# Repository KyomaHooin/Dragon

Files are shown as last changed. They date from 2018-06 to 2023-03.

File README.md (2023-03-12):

DESCRIPTION

DragonFrame Arduino code for custom stepper device.

DIAGRAM

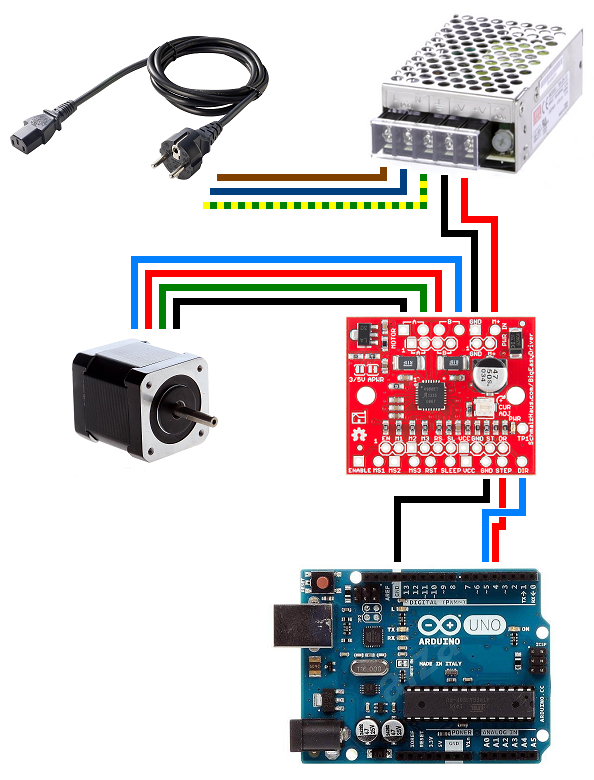
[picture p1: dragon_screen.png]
Dragon diagram


COMPONENT
<pre>
 1x <a href="https://laskarduino.cz/vyvojove-desky/100002-arduino-uno-r3-atmega328p-microusb-klon.html">Arduino Uno</a>(R3) 
 1x <a href="https://cnc.inshop.cz/krokove-motory-drivery/krokovy-motor-s-prirubou-nema17-0.44nm-typ-a">Nema 17 Stepper</a>(42STH47-1684A)
 1x <a href="https://www.aliexpress.com/item/2A-Phase-3D-Printer-Big-Easy-Driver-Board-V1-2-A4988-Stepper-Motor-Driver-Board-On/32834035739.html">Big Easy Driver</a>(ROB-12859) / <a href="https://arduino-shop.cz/arduino/1025-ramps1-4-drv8825-driver-pro-krokove-motory-1434305774.html">DRV8825</a> / (<a href="https://www.postavrobota.cz/Driver-pro-krokove-motory-A4988-d92.htm">A4988</a>)
 1x <a href="https://www.ges.cz/cz/zdroj-sitovy-prumyslovy-rs-25-12-GES07507650.html">Mean Well Supply</a> 12/2A(RS-25-12)
 3x <a href="https://www.ges.cz/cz/cpp-3-5-3bu-GES06614450.html">Terminal Block</a>(3BU 3.5mm)
 1x <a href="https://www.ges.cz/cz/nks-180-0-GES06914278.html">Supply Cable</a>
 1x <a href="http://www.hezkyden.cz/shop/hlinikovy-chladic-samolepici/">Driver Heatsink</a>(9x9x5mm)
10x <a href="https://www.ges.cz/cz/esst-m2-5x6-GES06814916.html">Screw Phillips Pan</a> M2.5x6(M2.5x4-5 = optimal)
 2x <a href="https://www.ges.cz/cz/skls-m3x6-GES06814931.html">Bolt Phillips Flat</a> M3x6(M3x4-5 = optimal)
 4x Screw Phillips Flat M3x30(M3x25 = optimal)
 5x <a href="https://www.ges.cz/cz/flexibilni-propojovaci-kabely-sd-j-10-GES07713790.html">Dupont cable</a>(MM)
 1x <a href="https://www.ges.cz/cz/mpfk-4-s-GES06900296.html">Phone 4Wire Flat</a>(1m)
 1x <a href="https://www.ges.cz/cz/wb-2x6-4bi-GES06614365.html">Coupler</a>(RJ11)
 2x <a href="https://www.ges.cz/cz/mp-6-4-GES06600690.html">Plug</a>(RJ11)
</pre>
FILE
<pre>
        openscad/ - Custom 3D printable box.
dragon_screen.png - Color connection schematic.
       DFMoco.ino - Original code by DragonFrame.
</pre>
SOURCE

https://github.com/KyomaHooin/Dragon

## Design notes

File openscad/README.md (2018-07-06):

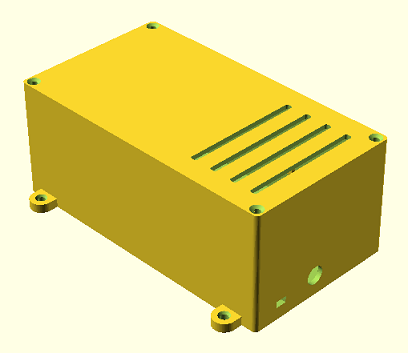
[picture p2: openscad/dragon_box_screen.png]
Dragon box


DESCRIPTION

DragonFrame Moco custom motor control box.

FILE
<pre>
              schema/ - Schematic directory.
          dragon.scad - SCAD model.
       dragon_top.stl - Top part STL.
    dragon_bottom.stl - Bottom part STL.
    dragon_bridge.stl - Bridge part STL.
dragon_box_screen.png - Box screenshot.
</pre>
SOURCE

https://github.com/KyomaHooin/Dragon

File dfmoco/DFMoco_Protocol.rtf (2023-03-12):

DFMoco Protocol

Version 2.0.0

Messages are given from perspective of DFMoco device.
Motor number starts at 1.
All positions are in steps. Dragonframe converts between step count and units.

Protocol
Serial Port (Comm)
Speed: 57600 Baud
Data bits: 8
Stop bits: 1
Parity: 0

Message Format
Messages are in ASCII text, with trailing \r\n

Messages

Hello (hi) - initiate communication
IN: hi
OUT: hi <major version> <number of axes> <full version string>
EXAMPLE: hi 1 8 1.2.7

Motor Status (ms) - check moving status of all motors
IN: ms
OUT: ms <0 or 1 for each motor, 1 = moving>
EXAMPLE: ms 10000000

Move Motor (mm) - move a motor to a position
IN: mm <motor> <step position>
EXAMPLE: mm 1 250
OUT: mm <motor> <target step position>
OUT2: mp <motor> <step position>
EXAMPLE: mm 1 250 (if motor needs to move)
EXAMPLE: mp 1 250 (if motor was already there)

Motor Position Query (mp) - request motor position
IN: mp <motor>
OUT: mp <motor> <step position>

Stop Motor (sm) - stop a motor fairly quickly
IN: sm <motor>
EXAMPLE: sm 1
OUT: sm <motor>
EXAMPLE: sm 1

Stop All (sa) - stop all motors fairly quickly
IN: sa
OUT: sa

Jog Motor (jm) - move the motor at a reasonable speed (pulse rate) towards destination
IN: jm <motor> <destination> [<velocity>]
OUT: jm <motor>

Note: velocity will be passed as a third argument if the major version in the hi response is 2 or greater. It is a positive number between 0 and 10000, with 10000 meaning to run at 100% of pulse rate.

Inch Motor (im) - move the in very small increments towards destination
IN: im <motor> <destination>
OUT: im <motor>

Pulse Rate (pr) - set the maximum steps/second of motor
IN: pr <motor> <steps/second>
EXAMPLE: pr 1 20000
OUT: pr <motor> <steps/second>

Zero Motor (zm) - resets the motor's current position to zero (no movement)
IN: zm <motor>
OUT: zm <motor>

New Position (np) - sets the motor's current position to a new value (no movement)
IN: np <motor> <position>
OUT: np <motor> <position>

Go-Motion (Blur):
This is complicated, and not required.
The goal is to capture a single frame, with the camera moving over a certain area while the shutter is open.

IN: bf <exposure time ms> <blur 0-1000> [ch#1 number] [ch#1 p0] [ch#1 p1] [ch#1 p2] [ch#2 number] [ch#2 p0] [ch#2 p1] [ch#2 p2] [etc]
OUT: bf 1000
Explanation:
The exposure time is how long the camera will be exposing the image.
The blur amount is in the range 0-1000, where 500 would correspond to a 50% or 180 degree blur setting (standard).
Then, for each motor that should move you receive four parameters:
1. A channel number.
2. A previous frame position value.
3. A current frame position value.
4. A next frame position value.

Each motor's movement should be centered around p1, such that:
The distance that is traveled is in relation to the blur percent (with 500 being 50%). 100% would mean the exposure happens for the entire distance of p0->p1->p2.
For 50% (the more standard case), the exposure happens at half the distance between p1 and the previous and next positions.
In mathematical terms, the exposure happens between these positions:
[p1 - (p1 - p0) * blurPercent] -> [p1] -> [p1 + (p2 - p1) * blurPercent]

And the exposure time should be evenly split between the two segments.
So it should take 1/2 of the exposure time to travel [p1 - (p1 - p0) * blurPercent] -> [p1] ,
and 1/2 of the exposure time to travel [p1] -> [p1 + (p2 - p1) * blurPercent]

Furthermore, there should be a ramp up to speed before the exposure starts, and a slow down after it stops.
The ramp up to speed should take exactly 1 second, even if the device does not need to move. This is so that Dragonframe knows when to trigger the camera.

After the device calculates the go-motion move, it starts sending all motors into the initial position.
Dragonframe will check for motor movement, and when everything has stopped, it will issue a "go" command:
IN: go
OUT: go

At this point the rig should immediately start the go-motion move as described above.

Notes
Any time a motor is moving, the device should send occasional "mp" messages.
Dragonframe will keep requesting motor status (ms) until the movement is finished.

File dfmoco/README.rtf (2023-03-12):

Simple Motion Control with Dragonframe (DFMoco)

Overview
This sketch turns an Arduino or equivalent development board into a multi-axis
motion control signal generator. It is for use with the Arc motion control system in
Dragonframe 4. It generates step and direction signals, which can be sent to
stepper motor drivers.

Note: This is NOT a REAL TIME solution.
This is a simple, low cost, motion control solution for stop motion and time-lapse.
Dragonframe will move all of your motors to position for frame 1, then shoot, then
move all of your motors to position for frame 2.

If you need real-time moves you should check out the DMC-32:
https://www.dragonframe.com/product/dmc-32/

Choosing a Development Board
Throughout this document we refer to Arduino because it is the most well-known
small development board. You can actually use a variety of boards:

To control up to four axes, you can use:
- Arduino Uno
- Arduino Duemilanove
- Arduino 101

To control up to eight axes, you can use:
- Arduino Mega
- Arduino Mega 2560

Wiring the Arduino for Motion Control
The Arduino running the DFMoco sketch will generate step and direction signals for stepper motors.

If you already have stepper motor drivers, you can take these signals and wire them into a connector for those drivers.

If you do not have stepper motor drivers, and need to move relatively small stepper motors, you can wire the Arduino signals to an Big Easy Driver or comparable board. You will use one Big Easy Driver for each stepper motor.
https://www.sparkfun.com/products/10735 (http://www.sparkfun.com/products/10267)

Kill Switch
It is recommended to incorporate a pushbutton kill switch, especially for larger rigs. This will stop all motors and bypasses any communication issues between the computer and the Arduino.

The DFMoco sketch expects you to have a kill switch attached to PIN 2 (interrupt 0).
If you do NOT want a kill switch, you must comment out this line in the code
#define KILL_SWITCH_INTERRUPT 0

You comment it out by add two forward slashes at the start, so it looks like this
//#define KILL_SWITCH_INTERRUPT 0

You can reference the schematic (but not the code) on this page if you are not sure how to connect a pushbutton:
https://docs.arduino.cc/built-in-examples/digital/Button

Step/Direction Pin Configuration

Channel 1
PIN 4 step
PIN 5 direction
Channel 2
PIN 6 step
PIN 7 direction
Channel 3
PIN 8 step
PIN 9 direction
Channel 4
PIN 10 step
PIN 11 direction

Channel 5
PIN 28 step
PIN 29 direction
Channel 6
PIN 30 step
PIN 31 direction
Channel 7
PIN 32 step
PIN 33 direction
Channel 8
PIN 34 step
PIN 35 direction

Install the Arduino Software
If you haven't already done so, you will need to install the Arduino software:
Go to https://www.arduino.cc/en/software and download the Arduino Software for your OS.

Loading the DFMoco Program
Once the Arduino software is installed, and your development board is wired, you need to load the DFMoco program
(called a sketch in Arduino terminology) onto the board.

1. Launch the IDE that you previously installed.
2. Open "DFMoco.ino" located in this folder.
3. Set your specific board using the "Tools" menu, "Board" submenu.
4. "Verify" the sketch by pressing the play button on the top left of the Arduino program.
(Command-R on Mac, Control-R on Windows)
5. "Upload" the sketch by pressing the button with a right arrow pointing to some dots.
(Command-U on Mac, Control-U on Windows)

Connecting Dragonframe and the Arduino Board
Your board is ready to go. Now you can start using it with Dragonframe:
1. Start Dragonframe.
2. Create a new scene or open a previous one.
3. Select Connections... from the Scene menu.
4. Press Add Connection and choose DFMoco Arduino as the device type.
5. Select ArcMoco #1 (or #2, #3, #4).
6. Choose the appropriate serial port.
7. Press the Connect button.
8. Refer to the Dragonframe User Guide, "Motion Control" chapter, and to our online tutorials for further instructions.

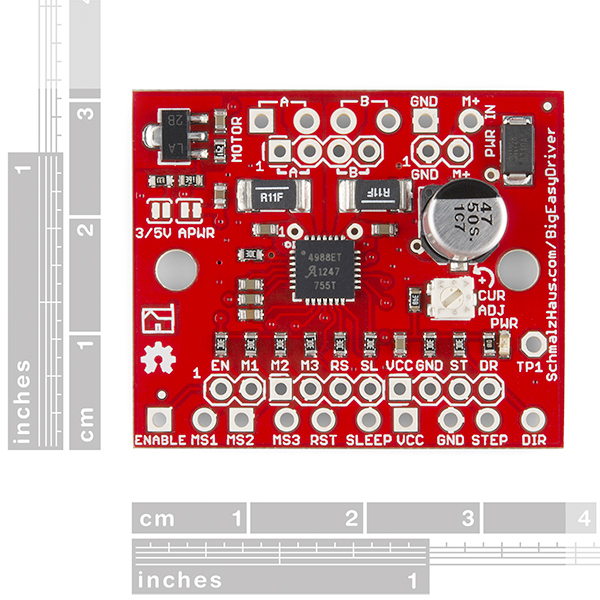
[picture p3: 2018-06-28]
openscad/schema/10735-02c.jpg

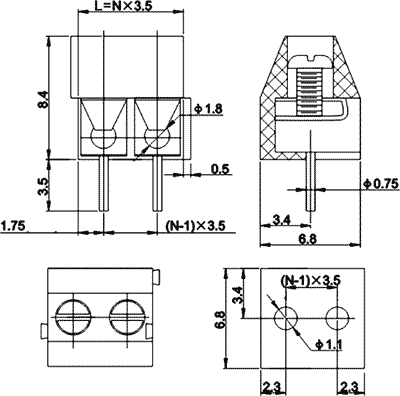
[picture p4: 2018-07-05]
openscad/schema/terminal.jpg

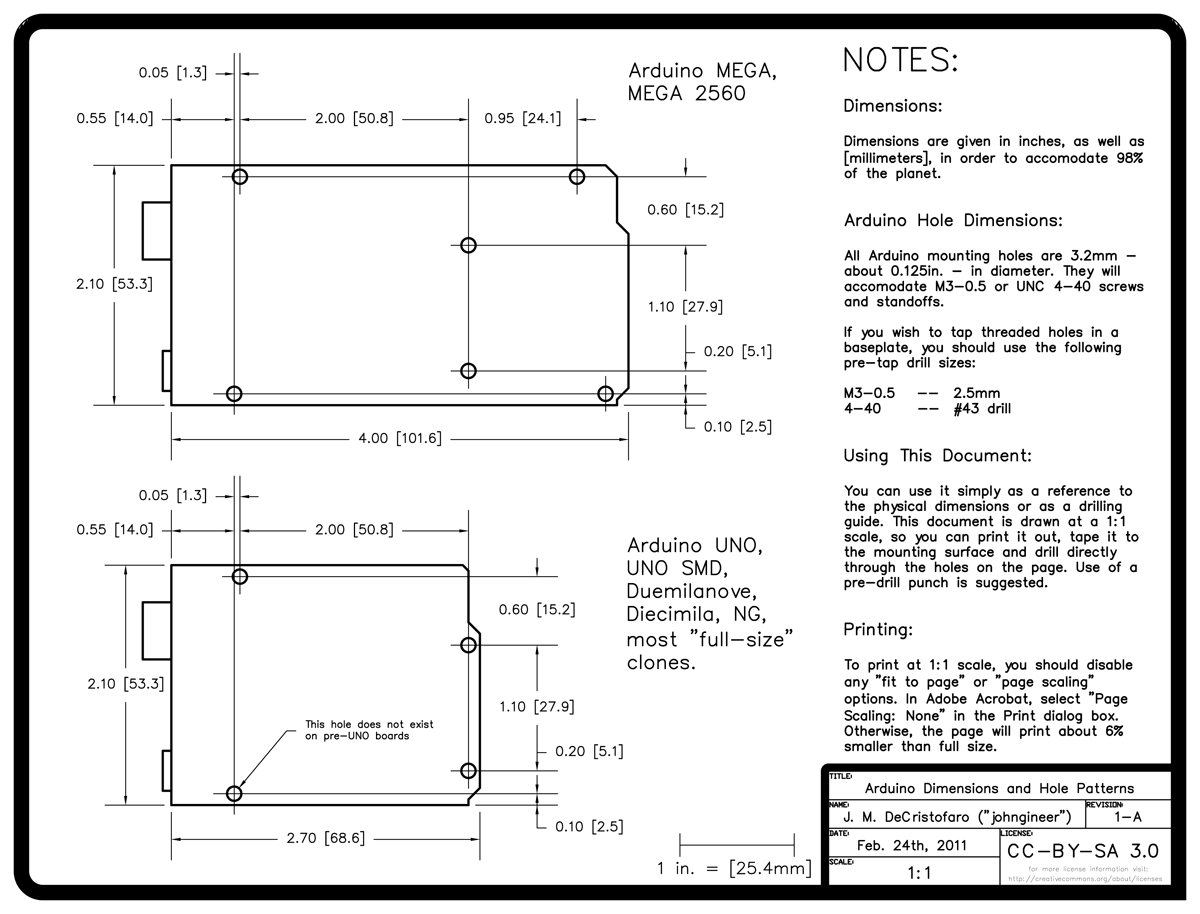
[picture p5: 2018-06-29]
openscad/schema/Arduino-Uno-Mega-Dimensions.png

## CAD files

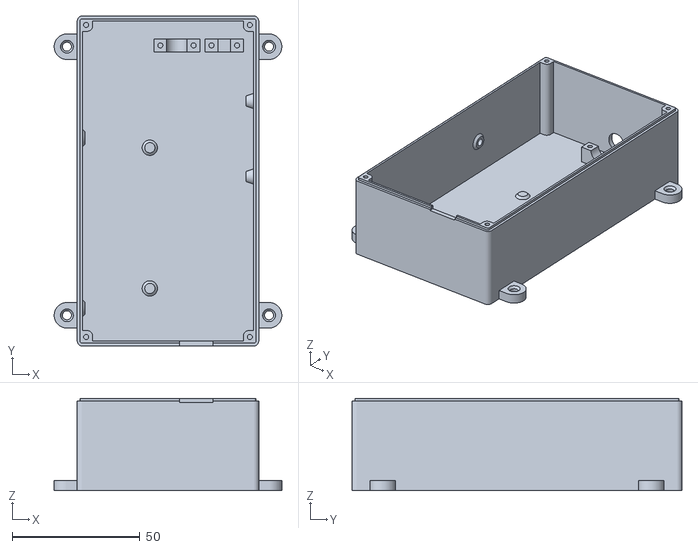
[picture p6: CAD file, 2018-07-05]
openscad/dragon_bottom.stl
89.0 x 129.0 x 36.0

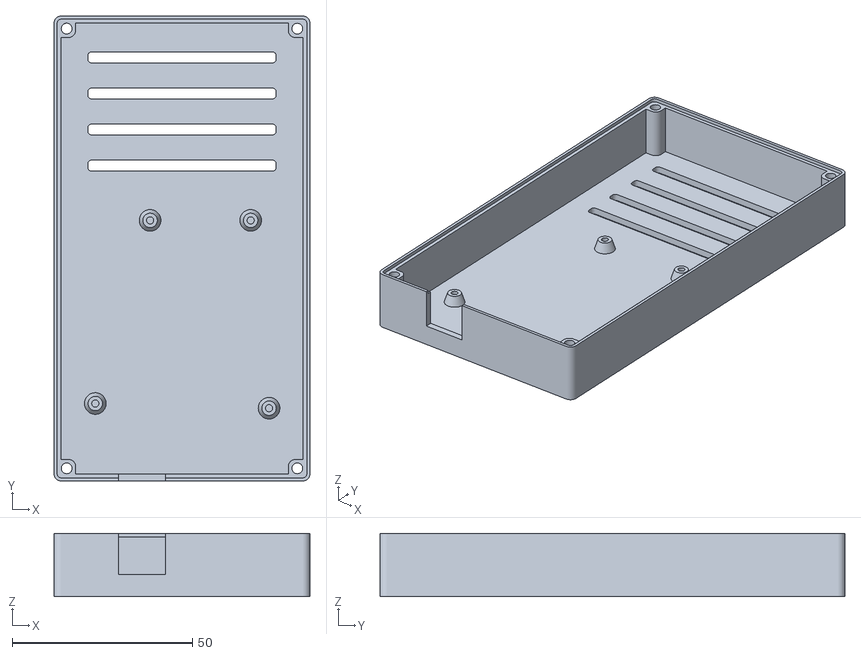
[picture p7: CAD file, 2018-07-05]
openscad/dragon_top.stl
71.0 x 129.0 x 17.5

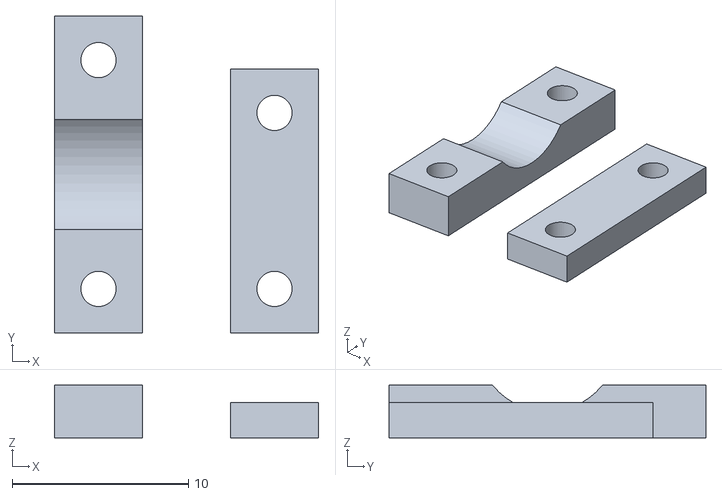
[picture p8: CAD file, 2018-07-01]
openscad/dragon_bridge.stl
15.0 x 18.0 x 3.00

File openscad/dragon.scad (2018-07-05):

//
// DragonFrame Motor Unit box
//

$fn=50;

drawTop=0;
drawBottom=0;
drawAll=0;
drawBridgePart=0;

//----------------------------

module rounded_rect(x, y, z, radius) {
    linear_extrude(height=z)
        minkowski() {
            square([x,y]);
            circle(r = radius);
        }
}

module mount(dia,thick) {
    difference() {
        cylinder(h=thick,d1=dia+4,d2=dia+2);
        translate([0,0,-1]) cylinder(h=thick+2,d=dia);
    }
}

module box_mount(thick,hole) {
    difference() {
    union() {
        cube([4,2,thick]);
        cube([2,4,thick]);
        translate([2,2,0]) cylinder(h=thick,d=4);
    }
    translate([1.5+0.01,1.5+0.01,-1]) cylinder(h=thick+2,d=hole);// Fold Bug
    }
}

module lip_lock_top() {
    rounded_rect(bottomX,bottomY,1,bottomThick/2+0.125);
}

module lip_lock_bottom() {
    difference() {
        rounded_rect(bottomX,bottomY,1,bottomThick);
        rounded_rect(bottomX,bottomY,1,bottomThick/2-0.125);
    }
}

module bridge() {
    difference() {
        cube([5,18,7]);
        translate([-1,9,7]) rotate([0,90,0]) cylinder(h=7,d=8);
        translate([2.5,2.5,3]) cylinder(h=5,d=2);
        translate([2.5,15.5,3]) cylinder(h=5,d=2);
    }
}

module bridge_motor() {
    difference() {
        cube([5,15,5]);
        translate([-1,5,3.5]) cube([7,5,2]);
        translate([2.5,2.5,1]) cylinder(h=5,d=2);
        translate([2.5,12.5,1]) cylinder(h=5,d=2);
    }
}

module bridge_part() {
    difference() {
        cube([5,18,3]);
        translate([-1,9,5.5]) rotate([0,90,0]) cylinder(h=7,d=8);
        translate([2.5,2.5,-1]) cylinder(h=5,d=2);
        translate([2.5,15.5,-1]) cylinder(h=5,d=2);
    }
    translate([10,0,0])
    difference() {
        cube([5,15,2]);
        translate([2.5,2.5,-1]) cylinder(h=5,d=2);
        translate([2.5,12.5,-1]) cylinder(h=5,d=2);
    }
}

module wall() {
    difference() {
        union() {
            cube([5,10,4]);
            translate([5,5,0]) cylinder(h=4,d=10);
        }
        translate([5,5,-1]) cylinder(h=6,d=3.5);
        translate([5,5,3])
        difference() {
            cylinder(h=1,d1=3.5,d2=5);
            cylinder(h=1,d=3.5);
        }
    }
}

module driver() {
    driverX=32;
    driverY=38;
    driverZ=1.3;
    difference() {
        color("darkgreen")
        translate([0,0,0]) cube([driverX,driverY,driverZ]);    
        translate([driverX/2,4.25,-1]) cylinder(h=driverZ+2,d=3);// Mount hole
        translate([driverX/2,driverY-4.25,-1]) cylinder(h=driverZ+2,d=3);
    }
    color("black") {
        translate([0,driverY/4,driverZ]) cube([6.6,22,8.4]);// Header M/PWR
        translate([driverX-6.6,driverY-11-driverY/8,driverZ]) cube([6.6,11,8.4]);// Header
    }
    color("silver")
    translate([driverX-20,driverY-8,driverZ]) cylinder(h=5.5,d=6);// Header
}

module uno() {
    unoX=53.3;
    unoY=68.6;
    unoZ=1.6;
    difference() {
        color("darkgreen")
        translate([0,0,0]) cube([unoX,unoY,unoZ]);    
        translate([unoX-2.5-5.1-27.9-15.2,14+1.3,-1]) cylinder(h=unoZ+2,d=3);// Mount Hole
        translate([unoX-2.5-5.1-27.9,14+1.3+50.8,-1]) cylinder(h=unoZ+2,d=3);
        translate([unoX-2.5-5.1,14+1.3+50.8,-1]) cylinder(h=unoZ+2,d=3);
        translate([unoX-2.5,14,-1]) cylinder(h=unoZ+2,d=3);
    }
    color("black") {
        translate([9.6-0.5,-6.2,unoZ-0.5]) cube([12+1,15,10.9+1]);// USB-B
        translate([unoX-2.5-5.1-27.9-15.2-2.54/2,25,unoZ]) cube([2.54,40,10]);// Header
        translate([unoX-2.5-2.54/2,35,unoZ]) cube([2.54,30,10]);
    }
}

module supply() {
    supplyX=51;
    supplyY=78;
    supplyZ=28;
    color("silver")
    translate([0,0,0]) cube([supplyX,supplyY,supplyZ]);
    color("black")
    translate([0,supplyY,supplyZ/4]) cube([51,14,14]);// Header
}

bottomX=65+2;
bottomY=125;
bottomZ=35;
bottomThick=2;

module bottom() {
    difference() {
        union() {
        difference() {
        translate([0,0,0]) rounded_rect(bottomX,bottomY,bottomZ+1,bottomThick);// BASE
        translate([0,0,bottomThick]) cube([bottomX,bottomY,bottomZ]);// FILL
        }
        translate([25.4+1,10.5+10,bottomThick]) cylinder(h=1,r1=3,r2=2);// Supply mount - bottom
        translate([25.4+1,10.5+55+10,bottomThick]) cylinder(h=1,r1=3,r2=2);
        }
        translate([-2,2.75+10,14+bottomThick+1]) rotate([0,90,0]) cylinder(h=4,d=3);
        translate([-2,2.75+66.5+10,14+bottomThick+1]) rotate([0,90,0]) cylinder(h=4,d=3);        
        translate([37,bottomY+2,bottomThick+7]) rotate([90,0,0]) cylinder(h=4,d=8);// Supply Hole
        translate([53,bottomY+2,bottomThick+3.5]) rotate([90,0,0]) cube([5,2.85,4]);// Motor Hole
        translate([0,0,bottomZ]) lip_lock_bottom();// Lip Lock
        translate([53.3+(topX-53.3)/2,6.2-bottomThick,bottomZ+topZ-topThick-3]) rotate([180,0,180]) uno();// Uno Cut
        translate([-bottomThick-0.1,2.75+10,14+bottomThick+1]) rotate([0,90,0]) cylinder(h=1.1,d1=5.5,d2=3);// Supply Sink
        translate([-bottomThick-0.1,2.75+66.5+10,14+bottomThick+1]) rotate([0,90,0]) cylinder(h=1.1,d1=5.5,d2=3);
    }
    translate([0-0.01,2.75+10,14+bottomThick+1]) rotate([0,90,0]) mount(3,1);// Supply mount - side
    translate([0-0.01,2.75+66.5+10,14+bottomThick+1]) rotate([0,90,0]) mount(3,1);
    translate([bottomX,60+4.25,16+bottomThick+9]) rotate([0,90,180]) mount(2,3);// Driver mount
    translate([bottomX,60+38-4.25,16+bottomThick+9]) rotate([0,90,180]) mount(2,3);
    translate([46,bottomY-12,bottomThick]) rotate([0,0,90]) bridge();// Supply Bridge
    translate([63,bottomY-12,bottomThick]) rotate([0,0,90]) bridge_motor();// Motor Bridge
    translate([0,0,2]) box_mount(bottomZ-1,2);// Bottom mount
    translate([bottomX,0,2]) rotate([0,0,90]) box_mount(bottomZ-1,2);
    translate([bottomX,bottomY,2]) rotate([0,0,180]) box_mount(bottomZ-1,2);
    translate([0-0.01,bottomY+0.01,2]) rotate([0,0,270]) box_mount(bottomZ-1,2);// NF Bug
    translate([bottomX+1,5,0]) wall();//Wall Mount
    translate([bottomX+1,bottomY-15,0]) wall();
    translate([-1,15,0]) rotate([0,0,180]) wall();
    translate([-1,bottomY-5,0]) rotate([0,0,180]) wall();
}

topX=65+2;
topY=125;
topZ=17.5;
topThick=2;
topUnoXOffset=(topX-53.3)/2;

module top() {
    difference() {
        translate([0,0,0]) rounded_rect(topX,topY,topZ,topThick);// BASE
        translate([0,0,-topThick]) cube([topX,topY,topZ]);// FILL
        translate([53.3+(topX-53.3)/2,6.2-topThick,topZ-topThick-3]) rotate([180,0,180]) uno();// Uno
        translate([1.5,1.5,topZ-3]) cylinder(h=topThick+2,d=3);//Top Mount Hole
        translate([topX-1.5,1.5,topZ-3]) cylinder(h=topThick+2,d=3);
        translate([1.5,topY-1.5,topZ-3]) cylinder(h=topThick+2,d=3);
        translate([topX-1.5,topY-1.5,topZ-3]) cylinder(h=topThick+2,d=3);
        for (vspace=[1:4])// Vent
            translate([topX/8,topY-10*vspace,topZ-topThick-1])rounded_rect(topX/8*6,1,topThick+2,1);
        translate(0,0,0) lip_lock_top();// Lip Lock
        translate([1.5,1.5,topZ-1]) cylinder(h=1,d1=3,d2=5.5);// Top Sink
        translate([topX-1.5,1.5,topZ-1]) cylinder(h=1,d1=3,d2=5.5);
        translate([1.5,topY-1.5,topZ-1]) cylinder(h=1,d1=3,d2=5.5);
        translate([topX-1.5,topY-1.5,topZ-1]) cylinder(h=1,d1=3,d2=5.5);
    }
    translate([2.5+topUnoXOffset,14+6.2-topThick,topZ-topThick]) rotate([0,180,0]) mount(2,3);// Uno Mount
    translate([2.5+5.1+topUnoXOffset,14+1.3+50.8+6.2-topThick,topZ-topThick]) rotate([0,180,0]) mount(2,3);
    translate([2.5+5.1+27.9+topUnoXOffset,14+1.3+50.8+6.2-topThick,topZ-topThick]) rotate([0,180,0]) mount(2,3);
    translate([2.5+5.1+27.9+15.2+topUnoXOffset,14+1.3+6.2-topThick,topZ-topThick]) rotate([0,180,0]) mount(2,3);
    translate([0,0,1]) box_mount(topZ-3,3);// Top Mount
    translate([topX,0,1]) rotate([0,0,90]) box_mount(topZ-3,3);
    translate([0,topY,1]) rotate([0,0,270]) box_mount(topZ-3,3);
    translate([topX+0.01,topY+0.02,1]) rotate([0,0,180]) box_mount(topZ-3,3);// strange bug?
}

//--------------------------

if (drawTop) {
    translate([topX+topThick,topThick,topZ]) rotate([0,180,0]) top();
}

if (drawBottom) {
    translate([bottomThick+9,bottomThick,0]) bottom();
}

if (drawBridgePart) {
    bridge_part();
}

if (drawAll) {
    bottom();
    translate([1,10,bottomThick+1]) supply();
    translate([bottomX-3,60,bottomThick+9]) rotate([0,0,0]) rotate([0,-90,0]) driver();
    translate([53.3+(topX-53.3)/2,6.2-bottomThick,bottomZ+topZ-topThick-3]) rotate([180,0,180]) uno();
    translate([0,0,bottomZ]) top();
}

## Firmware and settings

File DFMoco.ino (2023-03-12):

#define DFMOCO_VERSION 2
#define DFMOCO_VERSION_STRING "2.0.0"

/*
  DFMoco version 2.0.0
  
  Multi-axis motion control.
  For use with the Arc motion control system in Dragonframe 5.
  Generates step and direction signals, which can be sent to stepper motor drivers.
   
  Control up to four axes with an Uno, Duemilanove or 101 board.
  Control up to eight axes with a Mega or Mega 2560.

  Version History

  Version 2.0.0 Adds variable speed jogging for DF5
  Version 1.3.1 Report if go-motion speed cannot be reached.
  Version 1.3.0 Arduino 101 support. Remove non-Arduino support (chipKit, Maple).
  Version 1.2.7 Direction setup time.
  Version 1.2.6 Add PINOUT_VERSION option to use older pinout.
  Version 1.2.5 Fix jogging with low pulse rate.
  Version 1.2.4 Fix pin assignments
  Version 1.2.3 New Position command
  Version 1.2.2 Jog and Inch commands
  Version 1.2.1 Moved step/direction pins for motors 5-8.
                Detects board type automatically.
  Version 1.2.0 Basic go-motion capabilities
  Version 1.1.2 Smooth transitions when changing direction
  Version 1.1.1 Save/restore motor position
  Version 1.1.0 Major rework 
  Version 1.0.2 Moved pulses into interrupt handler
  Version 1.0.1 Added delay for pulse widths  
  Version 1.0.0 Initial public release.

  Getting Started:
  
   1. Install IDE (Integrated Development Environment):
      Go to https://www.arduino.cc/en/software and download the Arduino Software for your OS.
   2. Run the IDE you installed.
   3. Open this file in the IDE.
   4. Go to the Tools menu of the IDE and choose the Board type you are using.
   5. Verify/Compile the sketch. (Command-R on Mac, Control-R on Windows.)
   6. After this finishes, Upload the code to the board. (Command-U on Mac, Control-U on Windows.)
   

  Pin configuration:
  
  channel 1
        PIN   4   step
        PIN   5   direction
  channel 2
        PIN   6   step
        PIN   7   direction
  channel 3
        PIN   8   step
        PIN   9   direction
  channel 4
        PIN  10   step
        PIN  11   direction

  channel 5
        PIN  28   step
        PIN  29   direction
  channel 6
        PIN  30   step
        PIN  31   direction
  channel 7
        PIN  32   step
        PIN  33   direction
  channel 8
        PIN  34   step
        PIN  35   direction
 */

// change this to 1 if you want original pinout for channels 5-8
#define PINOUT_VERSION 2

/*
  This is PINOUT_VERSION 1
  
  channel 5
        PIN  22   step
        PIN  23   direction
  channel 6
        PIN  24   step
        PIN  25   direction
  channel 7
        PIN  26   step
        PIN  27   direction
  channel 8
        PIN  28   step
        PIN  29   direction
*/

// detect board type
#if defined(__AVR_ATmega1280__) || defined(__AVR_ATmega2560__)
  #define BOARD_MEGA 1
#elif defined(__AVR_ATmega328P__) || defined(__AVR_ATmega328__)  || defined(__AVR_ATmega168__)
  #define BOARD_UNO 1
#elif defined(ARDUINO_ARCH_ARC32) // Intel Curie/101
  #define BOARD_101 1
  #include "CurieTimerOne.h"
#else
  #error Cannot identify board
#endif

// USER: if you want a kill switch, uncomment out the next line by removing the // characters
//#define KILL_SWITCH_INTERRUPT 0

#define SERIAL_DEVICE Serial

#if defined(BOARD_101)
  #define PIN_ON(port, pin)  { digitalWrite(pin, 1); }
  #define PIN_OFF(port, pin) { digitalWrite(pin, 0); }
#else
  #define PIN_ON(port, pin)  { port |= pin; }
  #define PIN_OFF(port, pin) { port &= ~pin; }
#endif

// Arduino Uno/Duemilanove  -> 4 MOTORS MAX
// Arduino Mega 2560 / Mega -> 8 MOTORS MAX
#if defined(BOARD_UNO) || defined(BOARD_101)
#define MOTOR_COUNT 4
#else
#define MOTOR_COUNT 8
#endif

#define TIME_CHUNK 50
#define SEND_POSITION_COUNT 20000

// update velocities 20 x second
#define VELOCITY_UPDATE_RATE (50000 / TIME_CHUNK)
#define VELOCITY_INC(maxrate) (max(1.0f, maxrate / 70.0f))
#define VELOCITY_CONVERSION_FACTOR 0.30517578125f /* 20 / 65.536f */

#define MAX_VELOCITY 20000

// setup step and direction pins
#if defined(BOARD_101)

  #define MOTOR0_STEP_PORT 0
  #define MOTOR0_STEP_PIN  4
  
  #define MOTOR1_STEP_PORT 0
  #define MOTOR1_STEP_PIN  6

  #define MOTOR2_STEP_PORT 0
  #define MOTOR2_STEP_PIN  8

  #define MOTOR3_STEP_PORT 0
  #define MOTOR3_STEP_PIN  10

#elif defined(__AVR_ATmega1280__) || defined(__AVR_ATmega2560__)

  #define MOTOR0_STEP_PORT PORTG
  #define MOTOR0_STEP_PIN  B00100000
  
  #define MOTOR1_STEP_PORT PORTH
  #define MOTOR1_STEP_PIN  B00001000

  #define MOTOR2_STEP_PORT PORTH
  #define MOTOR2_STEP_PIN  B00100000

  #define MOTOR3_STEP_PORT PORTB
  #define MOTOR3_STEP_PIN  B00010000

  #if ( PINOUT_VERSION == 2 )
  
    #define MOTOR4_STEP_PORT PORTA
    #define MOTOR4_STEP_PIN  B01000000
  
    #define MOTOR5_STEP_PORT PORTC
    #define MOTOR5_STEP_PIN  B10000000
  
    #define MOTOR6_STEP_PORT PORTC
    #define MOTOR6_STEP_PIN  B00100000
  
    #define MOTOR7_STEP_PORT PORTC
    #define MOTOR7_STEP_PIN  B00001000

  #elif ( PINOUT_VERSION == 1 )
  
    #define MOTOR4_STEP_PORT PORTA
    #define MOTOR4_STEP_PIN  B00000001
  
    #define MOTOR5_STEP_PORT PORTA
    #define MOTOR5_STEP_PIN  B00000100
  
    #define MOTOR6_STEP_PORT PORTA
    #define MOTOR6_STEP_PIN  B00010000
  
    #define MOTOR7_STEP_PORT PORTA
    #define MOTOR7_STEP_PIN  B01000000

  #endif

#elif defined(BOARD_UNO)

  #define MOTOR0_STEP_PORT PORTD
  #define MOTOR0_STEP_PIN  B00010000
  
  #define MOTOR1_STEP_PORT PORTD
  #define MOTOR1_STEP_PIN  B01000000

  #define MOTOR2_STEP_PORT PORTB
  #define MOTOR2_STEP_PIN  B00000001

  #define MOTOR3_STEP_PORT PORTB
  #define MOTOR3_STEP_PIN  B00000100

#endif



/**
 * Serial output specialization
 */
#if defined(UBRRH)
#define TX_UCSRA UCSRA
#define TX_UDRE  UDRE
#define TX_UDR   UDR
#else
#define TX_UCSRA UCSR0A
#define TX_UDRE  UDRE0
#define TX_UDR   UDR0
#endif
 
char txBuf[32];
char *txBufPtr;

#define TX_MSG_BUF_SIZE 16

#define MSG_STATE_START 0
#define MSG_STATE_CMD   1
#define MSG_STATE_DATA  2
#define MSG_STATE_ERR   3

#define MSG_STATE_DONE  100

/*
 * Command codes from user
 */
#define USER_CMD_ARGS 40

#define CMD_NONE       0
#define CMD_HI         10
#define CMD_MS         30
#define CMD_NP         31
#define CMD_MM         40 // move motor
#define CMD_PR         41 // pulse rate
#define CMD_SM         42 // stop motor
#define CMD_MP         43 // motor position
#define CMD_ZM         44 // zero motor
#define CMD_SA         50 // stop all (hard)
#define CMD_BF         60 // blur frame
#define CMD_GO         61 // go!

#define CMD_JM         70 // jog motor
#define CMD_IM         71 // inch motor


#define MSG_HI 01
#define MSG_MM 02
#define MSG_MP 03
#define MSG_MS 04
#define MSG_PR 05
#define MSG_SM 06
#define MSG_SA 07
#define MSG_BF 10
#define MSG_GO 11
#define MSG_JM 12
#define MSG_IM 13


struct UserCmd
{
  byte command;
  byte argCount;
  int32_t args[USER_CMD_ARGS];
} ;

/*
 * Message state machine variables.
 */
byte lastUserData;
int  msgState;
int  msgNumberSign;
UserCmd userCmd;


struct txMsg
{
  byte msg;
  byte motor;
};

struct TxMsgBuffer
{
  txMsg buffer[TX_MSG_BUF_SIZE];
  byte head;
  byte tail;
};

TxMsgBuffer txMsgBuffer;


/*
 Motor data.
 */

uint16_t           motorAccumulator0;
uint16_t           motorAccumulator1;
uint16_t           motorAccumulator2;
uint16_t           motorAccumulator3;
#if MOTOR_COUNT > 4
uint16_t           motorAccumulator4;
uint16_t           motorAccumulator5;
uint16_t           motorAccumulator6;
uint16_t           motorAccumulator7;
#endif
uint16_t*          motorAccumulator[MOTOR_COUNT] =
{
  &motorAccumulator0, &motorAccumulator1, &motorAccumulator2, &motorAccumulator3, 
#if MOTOR_COUNT > 4
  &motorAccumulator4, &motorAccumulator5, &motorAccumulator6, &motorAccumulator7 
#endif
};

uint16_t           motorMoveSteps0;
uint16_t           motorMoveSteps1;
uint16_t           motorMoveSteps2;
uint16_t           motorMoveSteps3;
#if MOTOR_COUNT > 4
uint16_t           motorMoveSteps4;
uint16_t           motorMoveSteps5;
uint16_t           motorMoveSteps6;
uint16_t           motorMoveSteps7;
#endif
uint16_t*          motorMoveSteps[MOTOR_COUNT] =
{
  &motorMoveSteps0, &motorMoveSteps1, &motorMoveSteps2, &motorMoveSteps3,
#if MOTOR_COUNT > 4
  &motorMoveSteps4, &motorMoveSteps5, &motorMoveSteps6, &motorMoveSteps7
#endif
};


uint16_t           motorMoveSpeed0;
uint16_t           motorMoveSpeed1;
uint16_t           motorMoveSpeed2;
uint16_t           motorMoveSpeed3;
#if MOTOR_COUNT > 4
uint16_t           motorMoveSpeed4;
uint16_t           motorMoveSpeed5;
uint16_t           motorMoveSpeed6;
uint16_t           motorMoveSpeed7;
#endif
uint16_t         * motorMoveSpeed[MOTOR_COUNT] =
{
  &motorMoveSpeed0, &motorMoveSpeed1, &motorMoveSpeed2, &motorMoveSpeed3,
#if MOTOR_COUNT > 4
  &motorMoveSpeed4, &motorMoveSpeed5, &motorMoveSpeed6, &motorMoveSpeed7
#endif
};

volatile boolean nextMoveLoaded;


unsigned int   velocityUpdateCounter;
byte           sendPositionCounter;
boolean        hardStopRequested;

byte sendPosition = 0;
byte motorMoving = 0;
byte toggleStep = 0;


#define P2P_MOVE_COUNT 7

struct Motor
{
  byte   stepPin;
  byte   dirPin;

  // pre-computed move
  float   moveTime[P2P_MOVE_COUNT];
  int32_t movePosition[P2P_MOVE_COUNT];
  float   moveVelocity[P2P_MOVE_COUNT];
  float   moveAcceleration[P2P_MOVE_COUNT];

  float   gomoMoveTime[P2P_MOVE_COUNT];
  int32_t gomoMovePosition[P2P_MOVE_COUNT];
  float   gomoMoveVelocity[P2P_MOVE_COUNT];
  float   gomoMoveAcceleration[P2P_MOVE_COUNT];

  int       currentMove;
  float     currentMoveTime;
  
  volatile  boolean   dir;

  int32_t   position;
  int32_t   destination;
  float     maxVelocity;
  float     maxAcceleration;
  
  uint16_t  nextMotorMoveSteps;
  float     nextMotorMoveSpeed;

};

boolean goMoReady;
int     goMoDelayTime;

Motor motors[MOTOR_COUNT];

#ifdef KILL_SWITCH_INTERRUPT
void killSwitch()
{
  hardStopRequested = true;
}
#endif
      
/*
 * setup() gets called once, at the start of the program.
 */
void setup()
{
  goMoReady = false;
  lastUserData = 0;
  msgState = MSG_STATE_START;
  velocityUpdateCounter = 0;
  sendPositionCounter = 10;
  nextMoveLoaded = false;
  hardStopRequested = false;

  for (int i = 0; i < 32; i++)
    txBuf[i] = 0;
  
  txBufPtr = txBuf;
  
  #ifdef KILL_SWITCH_INTERRUPT
  attachInterrupt(KILL_SWITCH_INTERRUPT, killSwitch, CHANGE);
  #endif
  
  // initialize motor structures
  for (int i = 0; i < MOTOR_COUNT; i++)
  {
    // setup motor pins - you can customize/modify these after loop
    // default sets step/dir pairs together, with first four motors at 4/5, 6/7, 8/9, 10/11
    // then, for the Mega boards, it jumps to 28/29, 30/31, 32/33, 34/35
    #if ( PINOUT_VERSION == 2 )
      motors[i].stepPin = (i * 2) + ( (i < 4) ? 4 : 20 );
    #elif ( PINOUT_VERSION == 1 )
      motors[i].stepPin = (i * 2) + ( (i < 4) ? 4 : 14 );
    #endif
    
    motors[i].dirPin = motors[i].stepPin + 1;
    motors[i].dir = true; // forward
    motors[i].position = 0L;
    motors[i].destination = 0L;

    motors[i].nextMotorMoveSteps = 0;
    motors[i].nextMotorMoveSpeed = 0;
    
    setPulsesPerSecond(i, 5000);
  }


  // set output pins
  for (int i = 0; i < MOTOR_COUNT; i++)
  {
    pinMode(motors[i].stepPin, OUTPUT);
    pinMode(motors[i].dirPin, OUTPUT);
    
#if defined(__AVR_ATmega1280__) || defined(__AVR_ATmega2560__)

    // disable PWM
    switch (motors[i].stepPin)
    {
      #if defined(TCCR3A) && defined(COM3B1)
      case 4:
        TCCR3A &= ~COM3B1;
        break;
      #endif

      #if defined(TCCR4A) && defined(COM4A1)
      case 6:
        TCCR4A &= ~COM4A1;
        break;
      #endif

      #if defined(TCCR4A) && defined(COM4C1)
      case 8:
        TCCR4A &= ~COM4C1;
        break;
      #endif

      #if defined(TCCR2A) && defined(COM2A1)
      case 10:
        TCCR2A &= ~COM2A1;
        break;
      #endif
    }
    
#else
    
    switch (motors[i].stepPin)
    {
      #if defined(TCCR1A) && defined(COM1B1)
      case 10:
        TCCR1A &= ~COM1B1;
        break;
      #endif

    }

#endif
  }
  
  // set initial direction
  for (int i = 0; i < MOTOR_COUNT; i++)
  {
    digitalWrite( motors[i].dirPin, motors[i].dir ? HIGH : LOW );
  }

  // setup serial connection
  Serial.begin(57600);

  sendMessage(MSG_HI, 0);
    
  // SET UP interrupt timer  
  #if defined(BOARD_UNO) || defined(BOARD_MEGA)

    TCCR1A = 0;
    TCCR1B = _BV(WGM13);
  
    ICR1 = (F_CPU / 4000000) * TIME_CHUNK; // goes twice as often as time chunk, but every other event turns off pins
    TCCR1B &= ~(_BV(CS10) | _BV(CS11) | _BV(CS12));
    TIMSK1 = _BV(TOIE1);
    TCCR1B |= _BV(CS10);

  #elif defined(BOARD_101)

    CurieTimerOne.start(25, &updateStepDirection);

  #endif
}

#if defined(BOARD_101)
void updateStepDirection(void)
{
#else
ISR(TIMER1_OVF_vect)
{
#endif

  toggleStep = !toggleStep;
  
  if (toggleStep)
  {
    // MOTOR 1
    if (motorMoveSteps0)
    {
      uint16_t a = motorAccumulator0;
      motorAccumulator0 += motorMoveSpeed0;
      if (motorAccumulator0 < a)
      {
        motorMoveSteps0--;
        
        PIN_ON(MOTOR0_STEP_PORT, MOTOR0_STEP_PIN);
      }
    }

    // MOTOR 2
    if (motorMoveSteps1)
    {
      uint16_t a = motorAccumulator1;
      motorAccumulator1 += motorMoveSpeed1;
      if (motorAccumulator1 < a)
      {
        motorMoveSteps1--;
        
        PIN_ON(MOTOR1_STEP_PORT, MOTOR1_STEP_PIN);
      }
    }

    // MOTOR 3
    if (motorMoveSteps2)
    {
      uint16_t a = motorAccumulator2;
      motorAccumulator2 += motorMoveSpeed2;
      if (motorAccumulator2 < a)
      {
        motorMoveSteps2--;
        
        PIN_ON(MOTOR2_STEP_PORT, MOTOR2_STEP_PIN);
      }
    }

    // MOTOR 4
    if (motorMoveSteps3)
    {
      uint16_t a = motorAccumulator3;
      motorAccumulator3 += motorMoveSpeed3;
      if (motorAccumulator3 < a)
      {
        motorMoveSteps3--;
        
        PIN_ON(MOTOR3_STEP_PORT, MOTOR3_STEP_PIN);
      }
    }

#if MOTOR_COUNT > 4

    // MOTOR 5
    if (motorMoveSteps4)
    {
      uint16_t a = motorAccumulator4;
      motorAccumulator4 += motorMoveSpeed4;
      if (motorAccumulator4 < a)
      {
        motorMoveSteps4--;
        
        PIN_ON(MOTOR4_STEP_PORT, MOTOR4_STEP_PIN);
      }
    }

    // MOTOR 6
    if (motorMoveSteps5)
    {
      uint16_t a = motorAccumulator5;
      motorAccumulator5 += motorMoveSpeed5;
      if (motorAccumulator5 < a)
      {
        motorMoveSteps5--;
        
        PIN_ON(MOTOR5_STEP_PORT, MOTOR5_STEP_PIN);
      }
    }

    // MOTOR 7
    if (motorMoveSteps6)
    {
      uint16_t a = motorAccumulator6;
      motorAccumulator6 += motorMoveSpeed6;
      if (motorAccumulator6 < a)
      {
        motorMoveSteps6--;
        
        PIN_ON(MOTOR6_STEP_PORT, MOTOR6_STEP_PIN);
      }
    }

    // MOTOR 8
    if (motorMoveSteps7)
    {
      uint16_t a = motorAccumulator7;
      motorAccumulator7 += motorMoveSpeed7;
      if (motorAccumulator7 < a)
      {
        motorMoveSteps7--;
        
        PIN_ON(MOTOR7_STEP_PORT, MOTOR7_STEP_PIN);
      }
    }

#endif

  }
  else
  {
    velocityUpdateCounter++;
    if (velocityUpdateCounter == VELOCITY_UPDATE_RATE)
    {
      velocityUpdateCounter = 0;
      
      if (sendPositionCounter)
      {
        sendPositionCounter--;
      }
      
      for (int i = 0; i < MOTOR_COUNT; i++)
      {
        if (*motorMoveSpeed[i] && !motors[i].nextMotorMoveSpeed)
        {
          bitSet(sendPosition, i);
        }

        *motorMoveSteps[i] = motors[i].nextMotorMoveSteps;
        *motorMoveSpeed[i] = motors[i].nextMotorMoveSpeed;
        digitalWrite(motors[i].dirPin, motors[i].dir);

        *motorAccumulator[i] = 65535;
      }
      nextMoveLoaded = false; // ready for new move
    }
    
    PIN_OFF(MOTOR0_STEP_PORT, MOTOR0_STEP_PIN);
    PIN_OFF(MOTOR1_STEP_PORT, MOTOR1_STEP_PIN);
    PIN_OFF(MOTOR2_STEP_PORT, MOTOR2_STEP_PIN);
    PIN_OFF(MOTOR3_STEP_PORT, MOTOR3_STEP_PIN);

    #if MOTOR_COUNT > 4
      PIN_OFF(MOTOR4_STEP_PORT, MOTOR4_STEP_PIN);
      PIN_OFF(MOTOR5_STEP_PORT, MOTOR5_STEP_PIN);
      PIN_OFF(MOTOR6_STEP_PORT, MOTOR6_STEP_PIN);
      PIN_OFF(MOTOR7_STEP_PORT, MOTOR7_STEP_PIN);
    #endif
  }
}

/*
 * For stepper-motor timing, every clock cycle counts.
 */
void loop()
{
  int32_t *ramValues = (int32_t *)malloc(sizeof(int32_t) * MOTOR_COUNT);
  int32_t *ramNotValues = (int32_t *)malloc(sizeof(int32_t) * MOTOR_COUNT);

  for (int i = 0; i < MOTOR_COUNT; i++)
  { 
    if (ramValues[i] == ~ramNotValues[i])
    {
      motors[i].position = motors[i].destination = ramValues[i];
    }
  }  

  while (true)
  {
    if (!nextMoveLoaded)
      updateMotorVelocities();
    
    processSerialCommand();
    
    // check if we have serial output
    #if defined(BOARD_UNO) || defined(BOARD_MEGA)
    if (*txBufPtr)
    {
      if ((TX_UCSRA) & (1 << TX_UDRE))
      {
        TX_UDR = *txBufPtr++;
  
        // we are done with this msg, get the next one
        if (!*txBufPtr)
          nextMessage();
      }
    }
    #endif

    if (!sendPositionCounter)
    {
      sendPositionCounter = 20;

      byte i;
      for (i = 0; i < MOTOR_COUNT; i++)
      {
        if (bitRead(motorMoving, i) || bitRead(sendPosition, i))
        {
          sendMessage(MSG_MP, i);
          ramValues[i] = motors[i].position;
          ramNotValues[i] = ~motors[i].position;
        }
      }

      sendPosition = 0;
    }
  }
}

/**
 * Update velocities.
 */

void updateMotorVelocities()
{
  // process hard stop interrupt request
  if (hardStopRequested)
  {
    hardStopRequested = 0;
    hardStop();
  }
  
  for (int m = 0; m < MOTOR_COUNT; m++)
  {
    Motor *motor = &motors[m];
    motor->nextMotorMoveSteps = 0;
    motor->nextMotorMoveSpeed = 0;

    if (bitRead(motorMoving, m))
    {
      int seg = motor->currentMove;
      
      if (motor->moveTime[seg] == 0)
      {
        bitClear(motorMoving, m);
      }
      else
      {
        float originalMoveTime = motor->currentMoveTime;
        int originalMove = motor->currentMove;
        
        motor->currentMoveTime += 0.05f;
        
        if (motor->currentMoveTime >= motor->moveTime[seg])
        {
          motor->currentMoveTime -= motor->moveTime[seg];
          motor->currentMove++;
          seg++;
        }
        float t = motor->currentMoveTime;
        int32_t xn = (int32_t)(motor->movePosition[seg] + motor->moveVelocity[seg] * t + motor->moveAcceleration[seg] * t * t); // accel was already multiplied * 0.5

        int32_t dx = abs(xn - motor->position);

        if (!dx) // don't change direction flag unless we are actually stepping in new direction
          continue;
          
        boolean forward = xn > motor->position;

        if (forward != motor->dir) // direction setup time 1/20th second should be plenty
        {
          // revert everything except for dir flag
          motor->currentMoveTime = originalMoveTime;
          motor->currentMove = originalMove;
        }
        else
        {
          motor->nextMotorMoveSpeed = max(1, min(65535, dx * 65.6f));
          motor->nextMotorMoveSteps = dx;
          motor->position = xn;
        }
        
        motor->dir = forward;
      }      
    }
  }
  nextMoveLoaded = true;
}

/*
 * Set up the axis for pulses per second (approximate)
 */
void setPulsesPerSecond(int motorIndex, uint16_t pulsesPerSecond)
{
  if (pulsesPerSecond > MAX_VELOCITY)
    pulsesPerSecond = MAX_VELOCITY;
  if (pulsesPerSecond < 100)
    pulsesPerSecond = 100;
    
  motors[motorIndex].maxVelocity = pulsesPerSecond;
  motors[motorIndex].maxAcceleration = pulsesPerSecond * 0.5f;  
}


void setupMotorMove(int motorIndex, int32_t destination)
{
  motors[motorIndex].destination = destination;

  if (destination != motors[motorIndex].position)
  {
    calculatePointToPoint(motorIndex, destination);
    bitSet(motorMoving, motorIndex);
  }

}


void hardStop()
{
  // set the destination to the current location, so they won't move any more
  for (int i = 0; i < MOTOR_COUNT; i++)
  {
    stopMotor(i);
  }
}

void stopMotor(int motorIndex)
{
  int32_t delta = (motors[motorIndex].destination - motors[motorIndex].position);
  if (!delta)
    return;

  Motor *motor = &motors[motorIndex];
  int i;

  for (i = 0; i < P2P_MOVE_COUNT; i++)
  {
    motor->moveTime[i] = 0;
    motor->moveVelocity[i] = 0;
    motor->movePosition[i] = 0;
  }

  float v = VELOCITY_CONVERSION_FACTOR * motors[motorIndex].nextMotorMoveSpeed;
  float maxA = motor->maxAcceleration;
  float maxV = motor->maxVelocity;

  if (v > maxV)
    v = maxV;

  if (!motor->dir)
    v = -v;

  float t = fabs(v / maxA);

  motor->moveTime[0] = t;
  motor->movePosition[0] = motor->position;
  motor->moveVelocity[0] = v;
  motor->moveAcceleration[0] = (v > 0) ? -maxA : maxA;

  motor->moveTime[1] = 0;
  motor->movePosition[1] = (int32_t)(motor->movePosition[0] + motor->moveVelocity[0] * t + 0.5f * motor->moveAcceleration[0] * t * t);
  motor->moveVelocity[1] = 0;
  motor->moveAcceleration[1] = 0;

  motor->moveAcceleration[0] *= 0.5f;

  motor->destination = motor->movePosition[1];
  
  motor->currentMoveTime = 0;
  motor->currentMove = 0;  
}

boolean isValidMotor(int motorIndex)
{
  return (motorIndex >=0 && motorIndex < MOTOR_COUNT);
}


void processGoPosition(int motorIndex, int32_t pos)
{
  if (motors[motorIndex].position != pos)
  {
    setupMotorMove(motorIndex, pos);
    sendMessage(MSG_MM, motorIndex);
  }
  else
  {
    sendMessage(MSG_MP, motorIndex);
  }
}

/*

Command format

ASCII
[command two bytes]

Version
"hi"
-> "hi 1"

zero motor
"zm 1"
-> "z 1"

move motor
"mm 1 +1111111111

motor position?
mp 1

MOTOR STATUS
"ms"
-> "ms [busy motor count]"

SET PULSE PER SECOND
pr 1 200

STOP MOTOR
sm 1

STOP ALL
sa

*/
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

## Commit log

2018-06-28 Box init.
    [dragon.scad]
2018-06-29 Init update.
    [dragon.scad]
2018-06-29 Uno PLS resize, driver cap.
    [dragon.scad]
2018-06-29 Supply mount, driver mount.
    [dragon.scad]
2018-06-29 Code cleanup, Uno layout.
    [dragon.scad]
2018-06-29 Uno mount, typo.
    [dragon.scad]
2018-06-30 Box mount, vent.
    [dragon.scad]
2018-06-30 Vent tune.
    [dragon.scad]
2018-06-30 Lip lock.
    [dragon.scad]
2018-06-30 Lip lock fix.
    [dragon.scad]
2018-06-30 Sink holes.
    [dragon.scad]
2018-06-30 Sink render fix.
    [dragon.scad]
2018-06-30 Bridge better.
    [dragon.scad]
2018-06-30 Mount update.
    [dragon.scad]
2018-07-01 Mount fix, wall, bridge, cleanup update.
    [dragon.scad]
2018-07-01 Bridge part STL.
    [dragon_bridge.stl]
2018-07-01 Top part STL.
    [dragon_top.stl]
2018-07-01 Bottom part STL.
    [dragon_bottom.stl]
2018-07-01 Bottom part wall mount STL.
    [dragon_bottom_wall.stl]
2018-07-04 Supply cable.
2018-07-05 Supply mount update.
2018-07-05 Supply mount cleanup.
    [dragon.scad]
2018-07-05 Driver update.
    [dragon.scad]
2018-07-05 Terminal schematic.
2018-07-05 Driver mount update.
    [dragon.scad]
2018-07-05 Driver height update.
    [dragon.scad]
2018-07-05 Box width update.
    [dragon.scad]
2018-07-05 STL update.
    [dragon_bottom.stl, dragon_top.stl]
2018-07-05 Driver seller update.
2018-07-05 Driver mount fix.
    [dragon.scad]
2018-07-05 Fix driver mount.
    [dragon_bottom.stl]
2018-07-05 Screw URL update.
2018-07-06 Heatsink size.
